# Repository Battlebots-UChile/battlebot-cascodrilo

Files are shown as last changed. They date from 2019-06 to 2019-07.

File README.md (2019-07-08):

# Cascodrilo - 2019

Este proyecto se basa principalmente en generar un robot de combate, el cual, posea materiales reciclados, para que de esta forma sea amigable con el medioambiente, así el battlebot está diseñado con dos principales mecanismos, uno de ellos es la parte eléctrica, por lo que se utilizó el programa Arduino para llevar la mayoría de los movimientos a cabo. La otra es la parte mecánica, que funciona a la par con el sistema eléctrico, ya que se ocupan resortes, para conseguir más potencia en el arma del robot.

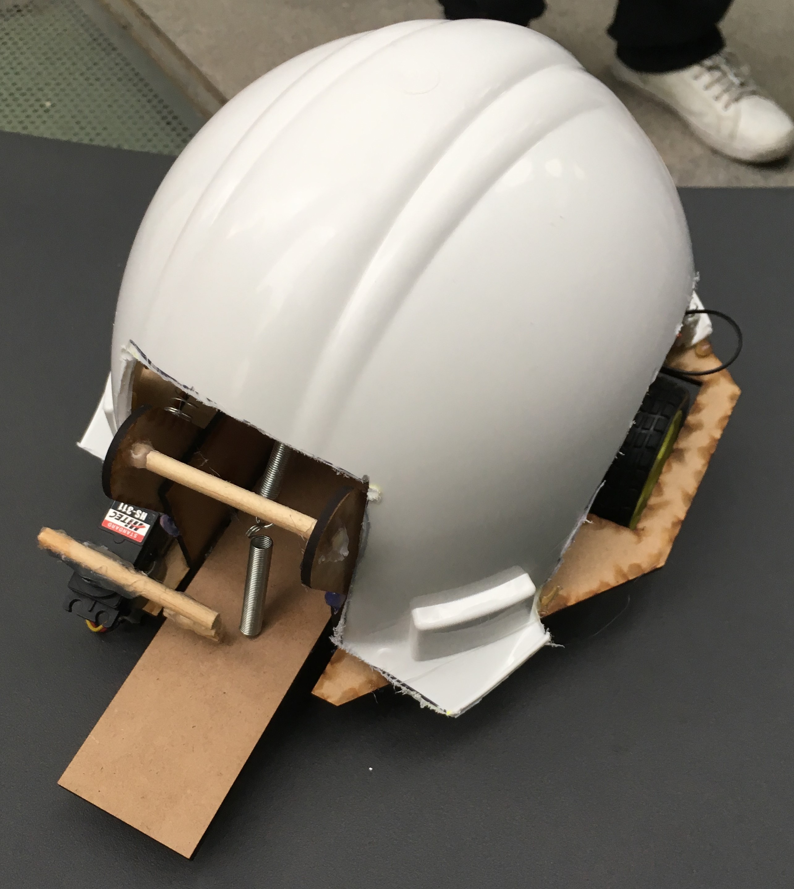
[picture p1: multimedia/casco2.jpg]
Cascodrilo


## Integrantes
- Jesús Cáceres - FCFM
- Karen Jara - FCFM
- Valentina Vásquez - FCFM
- Claudio Zúñiga - FCFM

## Descripción del proyecto

Inicialmente se describirá la forma y los componentes utilizados en la creación y formación del robot. Por lo que es importante destacar la restricciones presentes para la creación de este, así estas fueron, que pesara menos de 4.5 Kg, y que tuviera una altura, ancho, profundidad máxima de 30 cm cada una.
Es por ello que primeramente se pensó en qué arma utilizar, cuál sería la mejor estrategia de combate, ya que en función de esto se generaría la forma del robot. Por lo que se decidió por una palanca la cual estuviera con cierta inclinación del robot al suelo, de tal forma que los battlebots contrincantes quedaran arriba de esta, para que así, mediante cierta tracción esta palanca los impulsara hacia arriba, para que por efecto de la aceleración de gravedad caigan y se debiliten. Luego, se optó por una base similar a el Halcón milenario de Star Wars

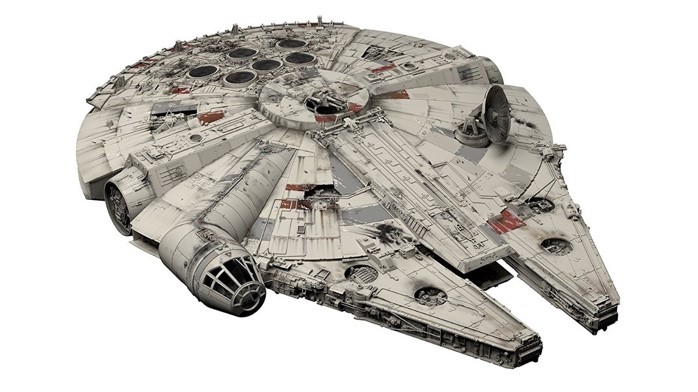
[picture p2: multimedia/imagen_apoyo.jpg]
Imagen de referencia


Ya que, en la fisura central se encuentra la palanca, la cual es traccionada mediante un servo y un resorte. En la parte de abajo, ya más cercana a la parte circular, posee dos ruedas, las cuales se controlan mediante dos motores DC, los cuales son independientes el uno del otro. Además posee una rueda cercano al lugar de la fisura, que es más pequeña que las otras dos, para que así le de una pequeña inclinación natural, y que de esta forma el battlebot alcance a robots de combate que sean más bajos a él. Lo que protege su interior (circuitos), es un casco, el cual, también lo protegerá de fuerzas externas que puedan dañarlo.

### Estrategia utilizada

#### Ofensiva
Su defensa es un casco, lo que inspiró el nombre, el cual se encarga de proteger el circuito y las partes electronicas del robot, en las peleas demostró ser bastante efectivo para protegerlo.

#### Defensiva
El robot intentará quedar de tal forma, que la palanca quede bajo el otro, para así impulsarlo hacia arriba y que caiga, en el mejor de los casos, que quede dado vuelta, para que así no tenga posibilidades de moverse y empujarlo hasta que caiga. Si bien el arma es bastante efectiva en la teoría, debido a que, la mayoría de los battlebots no presentan una defensa para este tipo de ataque, lo complejo es llevarlo a cabo, ya que la energía que se necesita es alta, y al no presentar un arma de defensa, es bastante propenso a ser destruido con las armas de los contrincantes.

### Diagrama funcional
Se adjuntan 3 imagenes con el diagrama de flujo

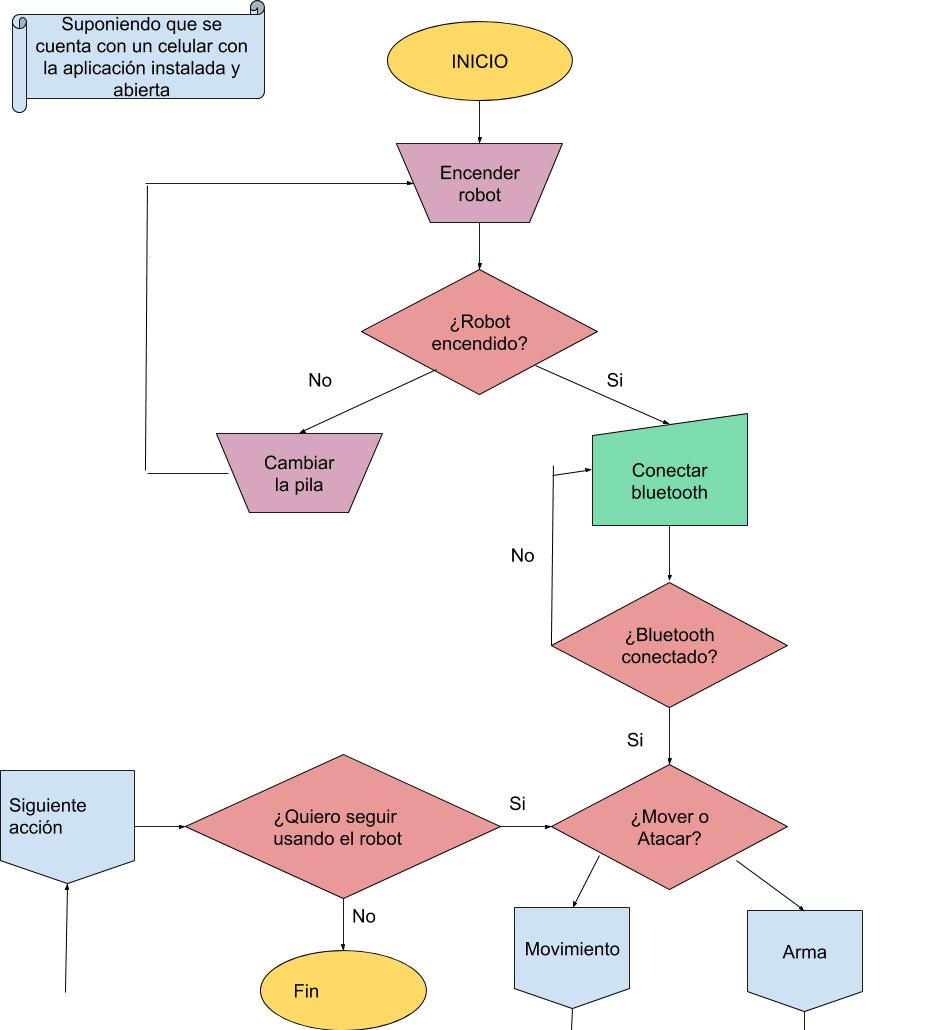
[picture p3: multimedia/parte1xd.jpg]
Parte1


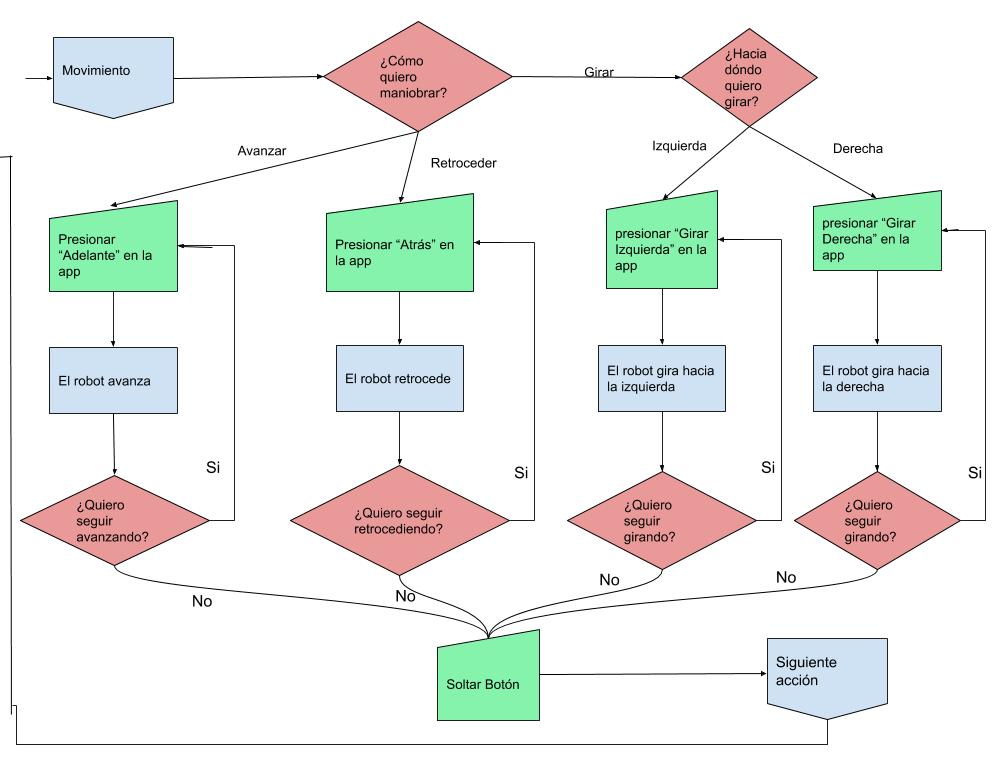
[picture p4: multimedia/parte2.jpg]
Parte2


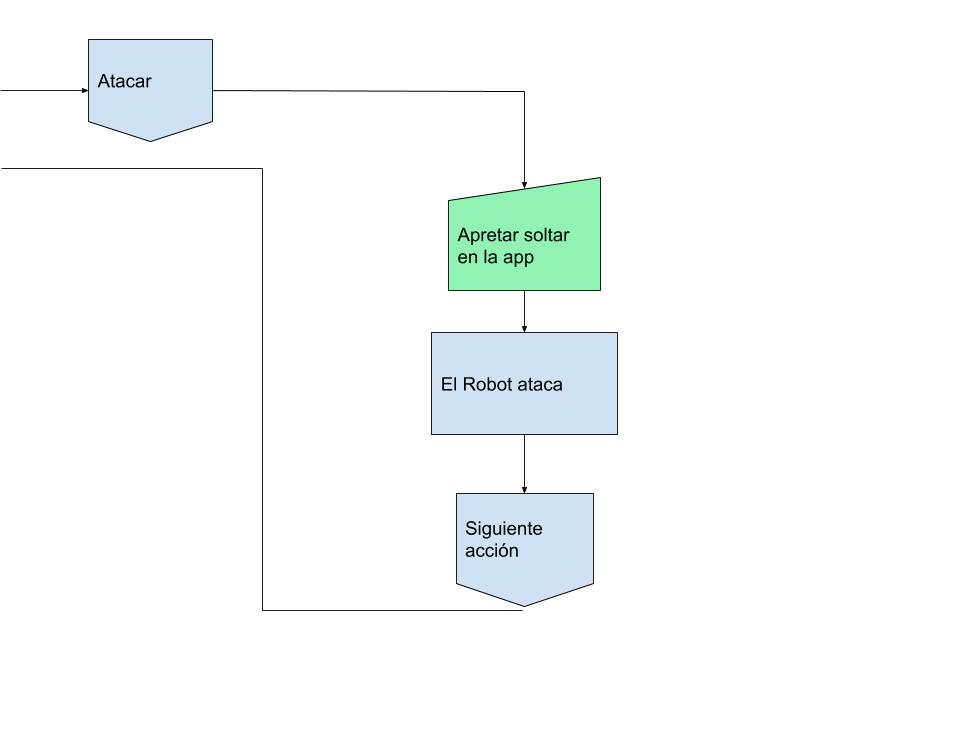
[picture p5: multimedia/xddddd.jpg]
Parte3


### Paso a Paso
Materiales a utilizar:
4 Baterías de 3.7V
1 Arduino Uno
2 Motores DC
2 Servo motores
Cables de arduino
Madera MDF 3mm
Madera MDF 5mm
Silicona caliente
Casco
Palos de maqueta
2 ruedas grandes
1 Rueda más pequeña

Instrucciones de armado.
1.	Diseñar e imprimir en cortadora laser las siguientes piezas:

Palanca [7,5x3]cm
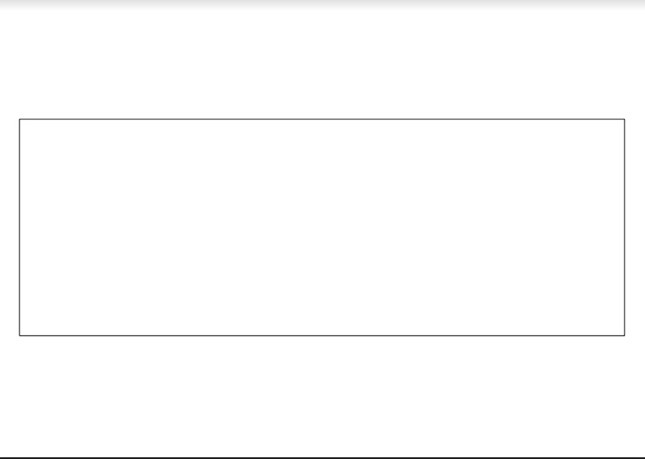
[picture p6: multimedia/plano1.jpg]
Palanca


Artefacto que alineará a la palanca para que esta no se salga de su eje, son necesarias 2 [4x2]cm
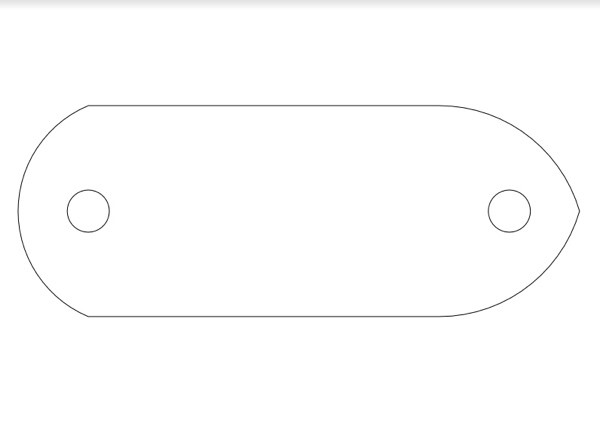
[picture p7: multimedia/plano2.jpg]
Cosa


Base en la cual se pondrán los circuitos [20x20]cm
los orificios son de 5 milimetros por 3 centímetros
y el sacado es de 5x3,5 cm
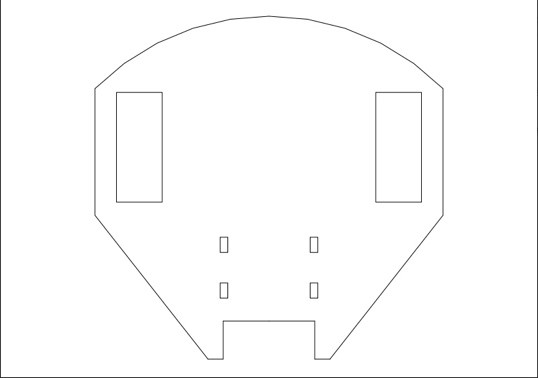
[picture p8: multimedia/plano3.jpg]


Soporte [4x2]cm, el agujero depende del tamaño de los palos de maqueta a utilizar
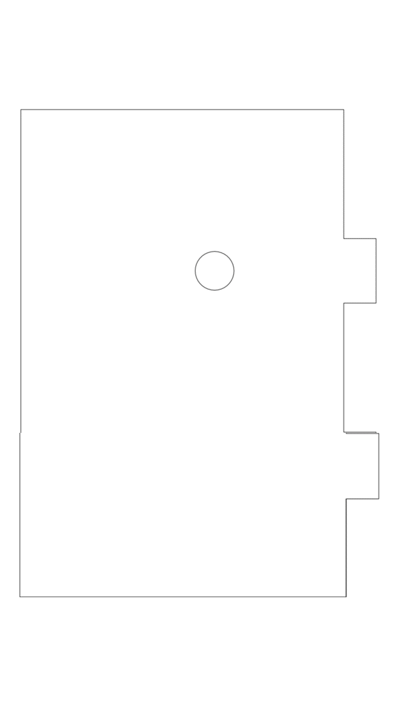
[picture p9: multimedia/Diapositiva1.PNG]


2.	Estas piezas están hechas para ser ensambladas con facilidad, por lo que, pondremos la base y la placa de soporte juntas, en los orificios que posee la primera, ubicaremos lo que sobresale de la segunda. Para que esto permanezca firme, lo pegaremos con silicona caliente.

3.	Una vez listo el paso anterior, ubicaremos los orificios de la placa de soporte (ya pegada a la base) con la lateral juntos, de tal forma que el palo de maqueta quepa en medio, así en un borde del palo de maqueta, colocamos una aureola de silicona caliente y esperamos a que se seque, con cuidado de no juntar el palo de maqueta con la placa, la función de esto es generar una especie de tope para no desalinear el movimiento, repetimos este paso para ambos lados, así cortamos lo que sobre de palo de maqueta y repetimos el colocar silicona el otro extremo.

4.	Luego, es posible notar que hay dos agujeros presenten en las piezas laterales, entre ellas debe haber un palo de maqueta que las una y atraviese tales hoyos, así debemos cortar la madera sobrante y pegar con silicona caliente.

5.	Luego colocar y pegar una bisagra en el centro, en medio del sacado grande, donde se encuentran ubicadas las piezas de soporte, y pegar un extremo de la palanca a ella, así la palanca debe estar bajo el palo de maqueta atravesado entre las dos placas.

6.  Lo siguiente que haremos es pegar un servo junto a la palanca, que quede en una de las aletitas de la base, con esto ubicamos un palo de maqueta que se mueva junto con el servo para regular el paso de la palanca.

7.  Para continuar ubicamos dos resortes juntos tales que sean movidos por un motor el cual estará sostenido por un palo de maqueta, que esté atrás de la placa de soporte, así el otro extremo del resorte debe quedar adherido a la palanca.

8.	Las ruedas se deben ubicar en los agujeros más grandes presentes en la base, estas deben estar ligadas a los motores DC, los cuales se encontraran pegados por abajo a la base.

9.	Cuando se haya ubicado el Arduino y lo complementario a este, dentro de el área basal, es posible pegar el casco el cual será cortado sin medidas precisas, sino que acomodándolo como mejor quede (el cómo van distribuidos los cables del arduino y las baterías está especificado en otra sección).

## Licencia
<br />Esta obra está bajo una <a rel="license" href="http://creativecommons.org/licenses/by-nc/4.0/">Licencia Creative Commons Atribución-NoComercial 4.0 Internacional</a>.

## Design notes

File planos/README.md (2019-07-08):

# Archivos de planos incluidos

Se adjunta archivo dxf con los planos de las piezas que se imprimen para la construcción del battlebot.

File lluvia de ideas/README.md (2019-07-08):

# Lluvia de Ideas

En este bosquejo pensamos en hacer un battlebot volador, por eso la cara de pajaro, que tuviera garras para atacar
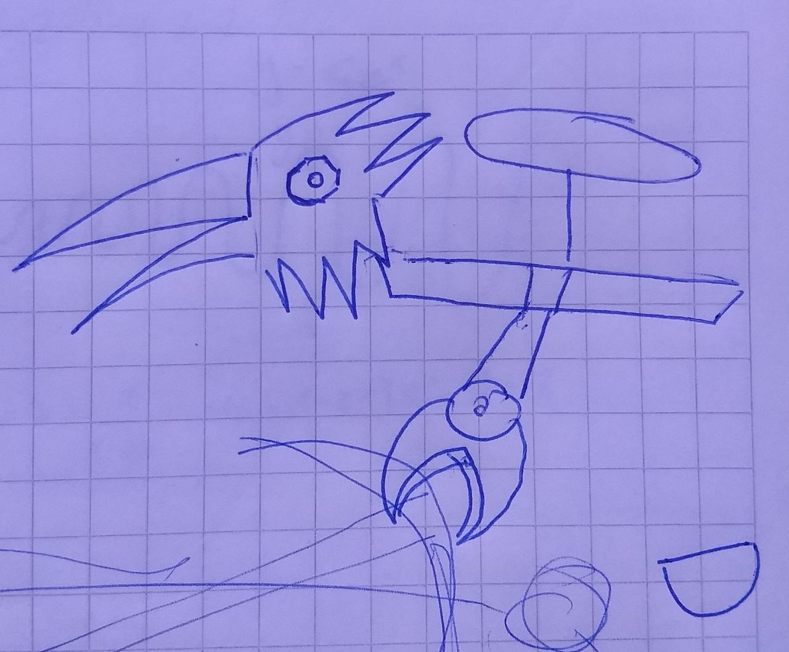
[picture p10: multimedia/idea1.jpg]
Idea1


La idea en este bosquejo era una especie de tortuga con una colo de puas como arma y unos brazoz adelante para impulzar hacia arriba a los enemigos.
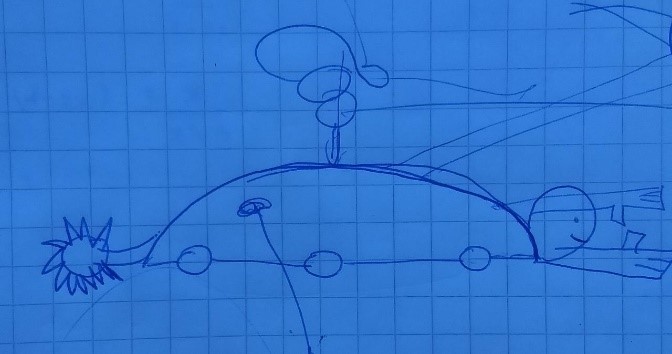
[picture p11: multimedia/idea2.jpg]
Idea2


En este bosquejo la idea era un battlebot circular con toperoles laterales de arma y resortes cubriendolo para amortiguar los golpes.
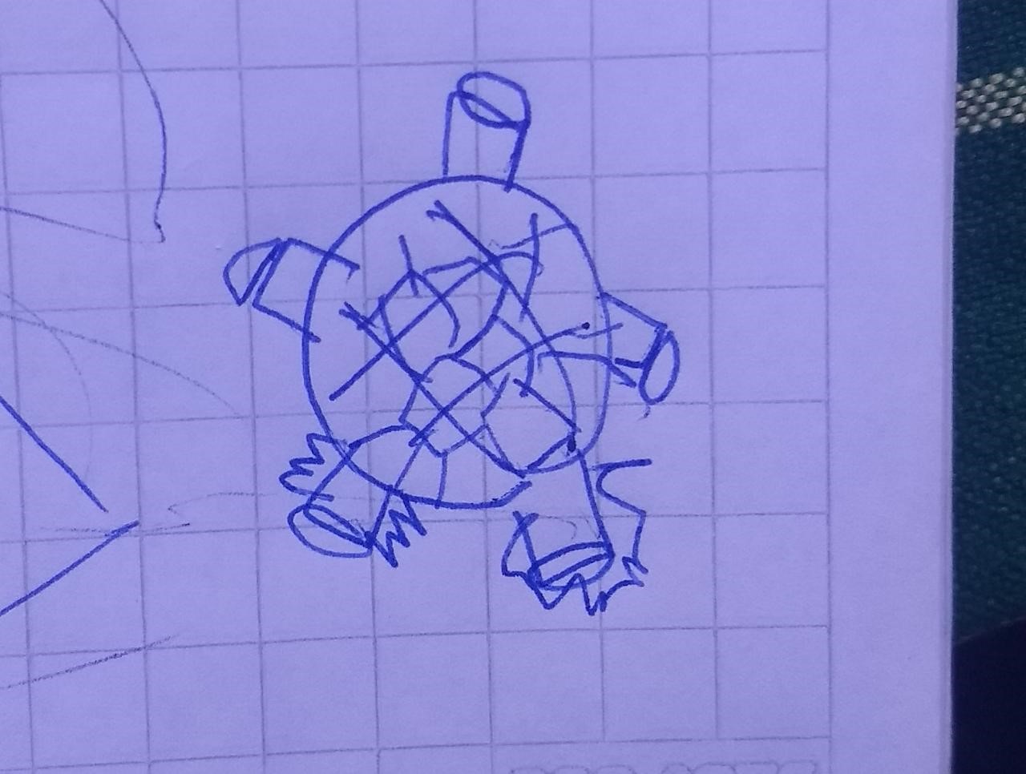
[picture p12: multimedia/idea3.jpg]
Idea3


La idea de este bosquejo era un battlebot alargado y cercano al suelo para aumentar la estabilidad.
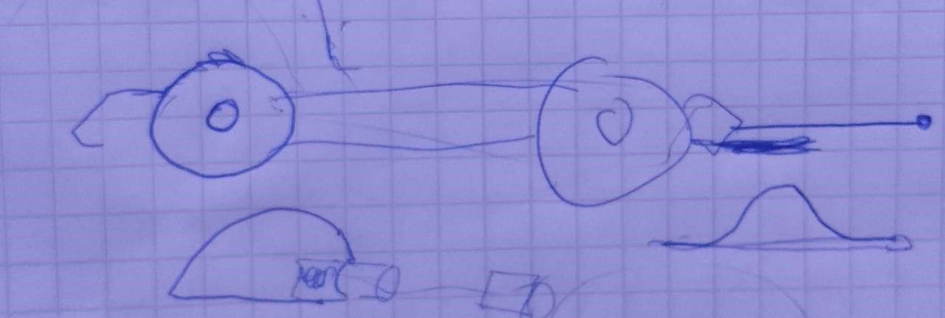
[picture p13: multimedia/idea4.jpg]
Idea4


Además vimos varios videos de peleas para sacar inspiración y de esos surgío la idea de que el arma fuera una especie de catapulta tomando a los otros battlebots de abajo y lanzarlos hacia arriba

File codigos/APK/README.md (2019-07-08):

# Código de la Aplicación

Para controlar al Cascodrilo, se utiliza el celular, el cual posee una aplicación que se conecta via Bluetooth, cual posee botones cuyos nombres indican cómo se moverá el robot. Este posee 7 botones; el llamado Adelante, hace avanzar al robot, Atrás, provoca que retroceda, el botón Girar a la derecha y el Girar a la izquierda, provocan que el robot rote en las respectivas direcciones antes mencionadas, los dos que quedan Estirar y Soltar están relacionados con la palanca, el primero genera que el resorte se estire y el soltar provoca que por el estiramiento del resorte la palanca se suelte, ya que el servo que lo mantiene fijo, se moverá para provocar que el arma se mueva.

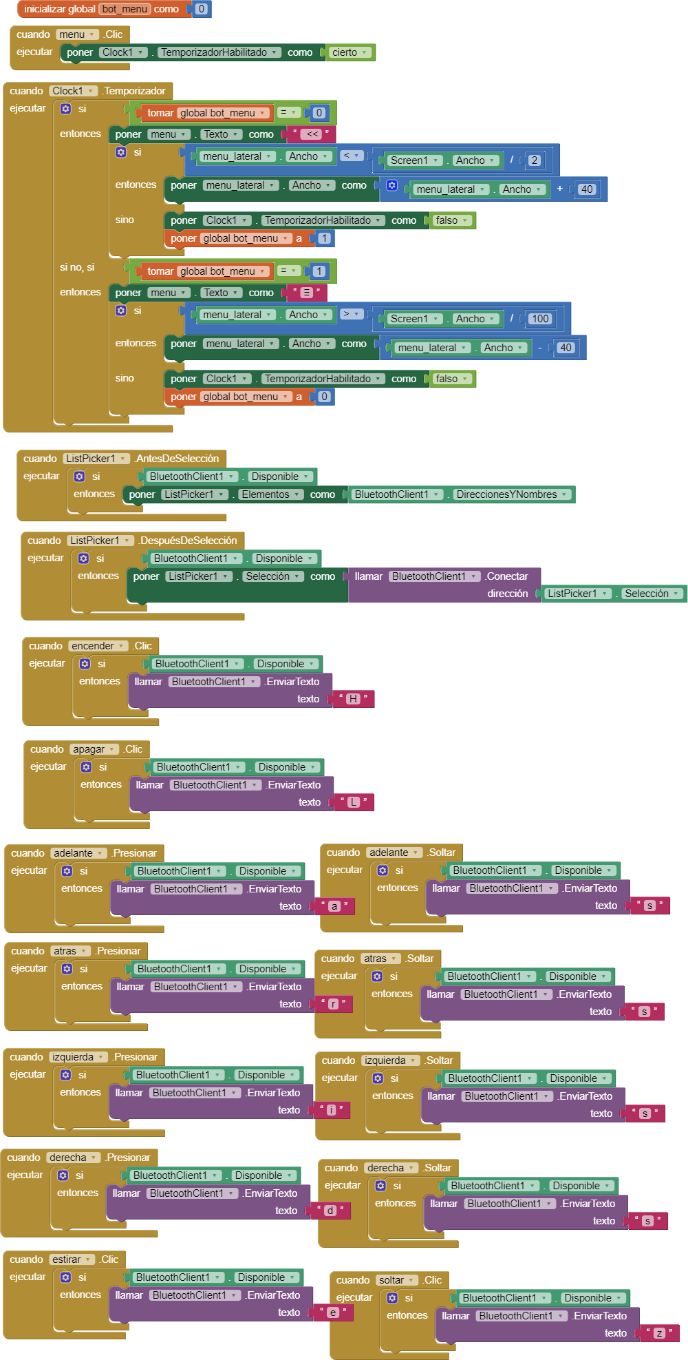
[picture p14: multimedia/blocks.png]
Aplicacion


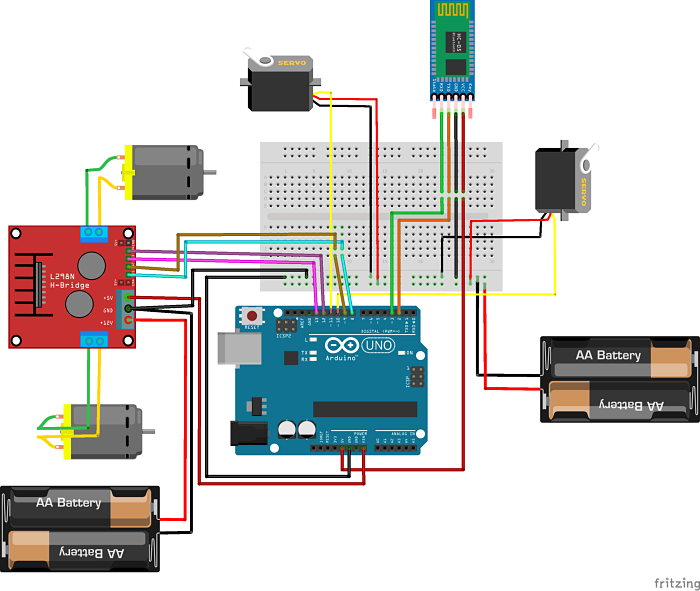
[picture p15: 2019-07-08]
diagrama/Proyecto Cascodrilo_bb_opt.png

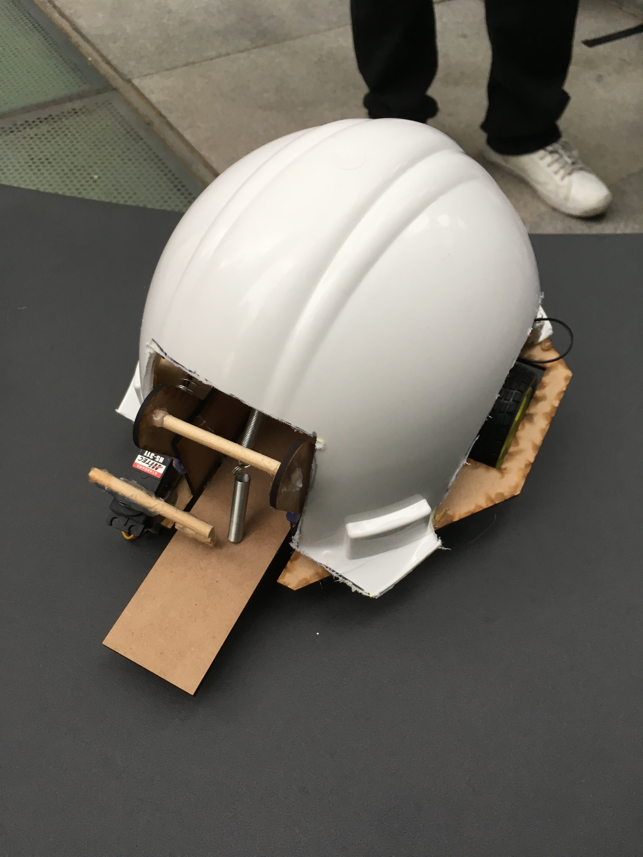
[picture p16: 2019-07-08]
multimedia/casco.JPG

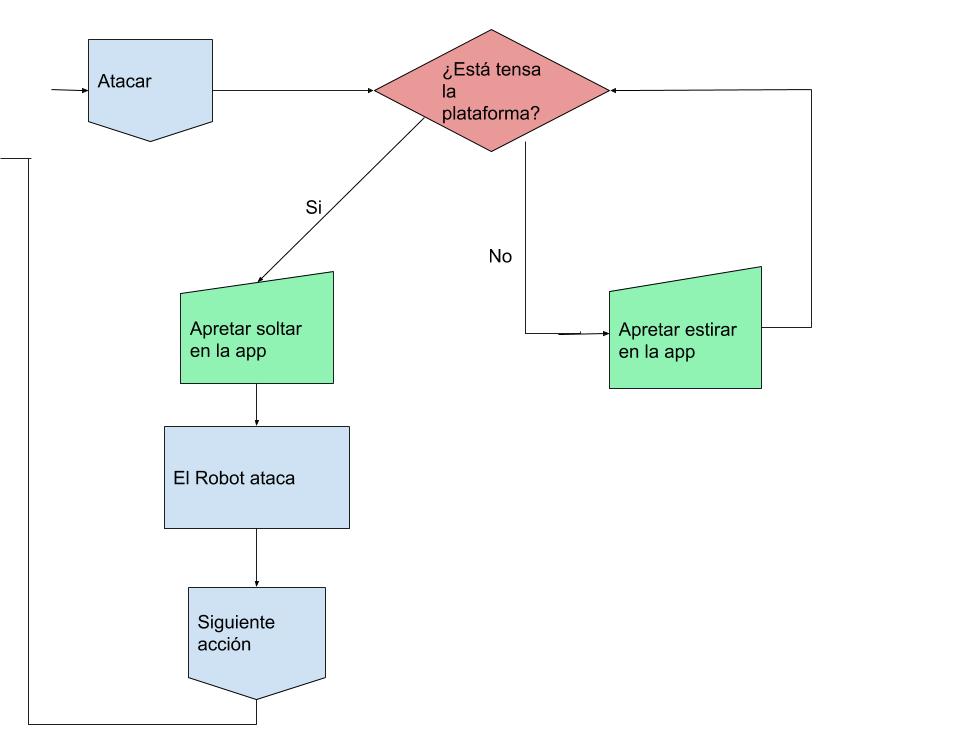
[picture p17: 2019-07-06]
multimedia/parte3.jpg

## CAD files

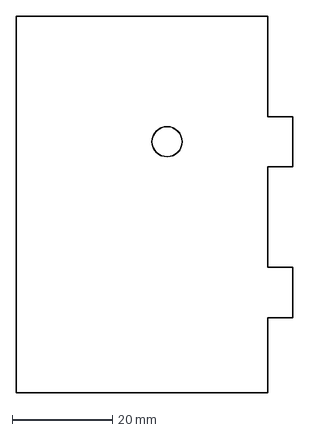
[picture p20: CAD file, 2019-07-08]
planos/Pieza lateral.dxf
55.0 x 75.0 mm

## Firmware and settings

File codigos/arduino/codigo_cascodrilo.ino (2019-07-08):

#include <Servo.h>
#include <SoftwareSerial.h>
SoftwareSerial BT(2,3);
Servo servo1;
Servo servo2;
int val;


void setup()
{
  BT.begin(9600);
  servo1.attach(10);
  servo2.attach(11);
  servo1.write(0);
  servo2.write(-90);

  //Declarar los pines para el motor 1
  pinMode(8, OUTPUT); //I1
  pinMode(9, OUTPUT); //I2

  //Declarar los pines para el motor 2
  pinMode(12, OUTPUT);  //I3
  pinMode(13, OUTPUT);  //I4

  delay(3000);

}

void loop()
{
  if (BT.available() >= 1)
  {
    val = BT.read();

    if (val == 'r')
    {
      motores(-250, 250);
    }
    else if (val == 'i')
    {
      motores(-250, -250);
    }
    else if (val == 's')
    {
      digitalWrite(8, LOW);
      digitalWrite(9, LOW);
      digitalWrite(12, LOW);
      digitalWrite(13, LOW);
    }
    else if (val == 'a')
    {
      motores(250, -250);
    }
    else if (val == 'd')
    {
      Disparo();
    }
  }
}

void motores(float m1, float m2)
{
  //m1 y m2 son las velocidades del primer
  // y segundo motor, entre -255 y 255




  //Invertir el giro del motor 1 si es necesario
  if (m1 < 0)
  {
    digitalWrite(13, HIGH);
    digitalWrite(12, LOW);
    m1 = -m1;
  }
  else
  {
    digitalWrite(13, LOW);
    digitalWrite(12, HIGH);
  }


  //Invertir el giro del motor 2 si es necesario
  if (m2 < 0)
  {
    digitalWrite(9, HIGH);
    digitalWrite(8, LOW);
    m2 = -m2;
  }
  else
  {
    digitalWrite(9, LOW);
    digitalWrite(8, HIGH);
  }

}

void Disparo()
{
  servo1.write(-90);
  delay(2000);
  servo2.write(0);
  delay(2000);
  servo1.write(0);
  delay(2000);
  servo2.write(-90);


}

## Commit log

2019-06-19 Actualizando archivos de la plantilla
2019-06-19 Agregando los nombres de los integrantes
2019-07-07 Codigo del arduino
2019-07-08 Cambié el diagrama por uo que estuviese de acuerdo con el código final
2019-07-08 Arreglo de conflicto
2019-07-08 fin con el readme principal
2019-07-08 terminando lluvias de ideas
2019-07-08 agregando planos
    [Pieza lateral.dxf]
